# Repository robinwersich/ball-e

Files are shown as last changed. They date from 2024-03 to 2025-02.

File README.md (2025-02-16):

# Ball-E

This robot was created during the **Robot Engineering Project** of the [University of Tartu](https://ut.ee/et) and aimed to build a robot that can [move and balance on a basketball](https://www.youtube.com/watch?v=eqhnZmMAU6M). The final result can be seen in action [here](https://drive.google.com/file/d/1LnrX0tRvga_g_EQCs7Uyl19VpnJzpEGV/preview).
The main concepts in the project explored are:
- use of omniwheels
- bluetooth remote control
- balancing control logic
- 3D printing
- hardware selection and wiring

<div>
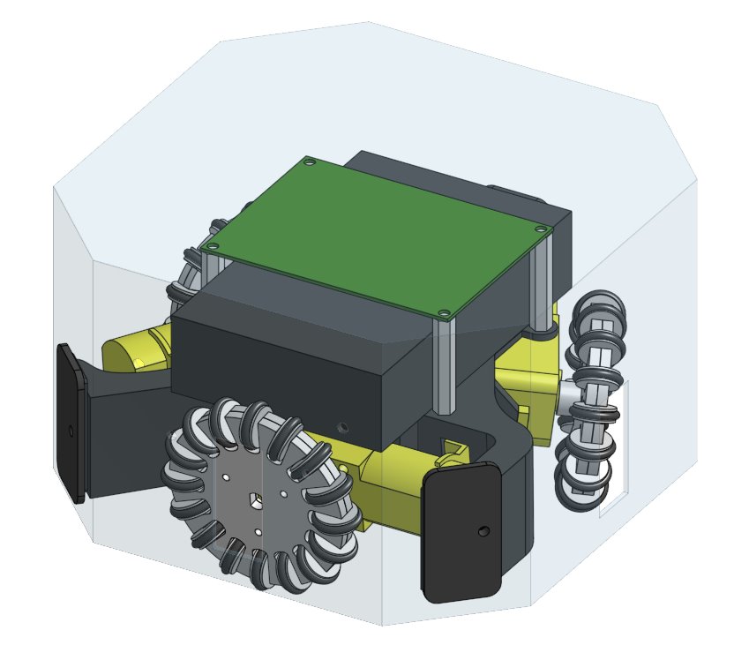
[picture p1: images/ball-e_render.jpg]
  
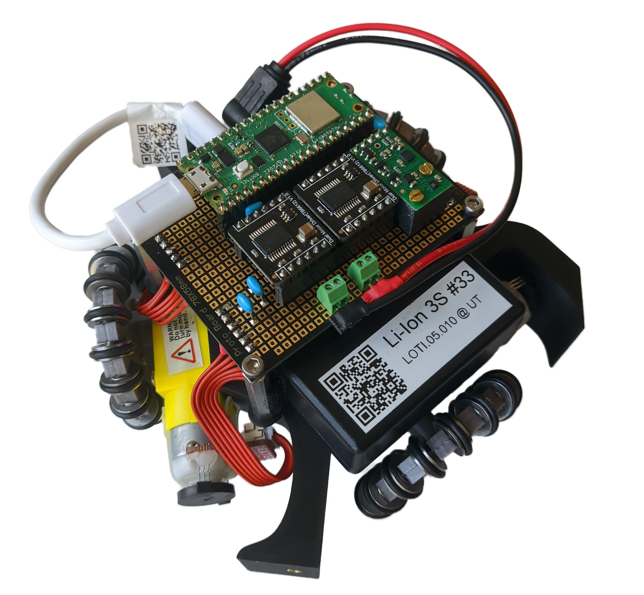
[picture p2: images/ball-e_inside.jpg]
  
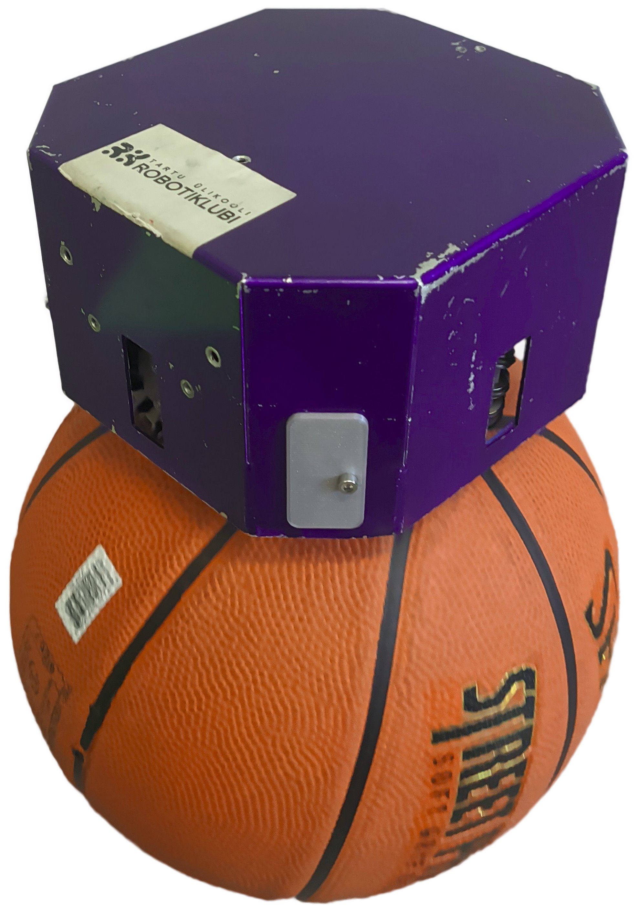
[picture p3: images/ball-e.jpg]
  
</div>

## Hardware BOM

- 3 [motors with encoders](https://gopigo.io/gopigo3-motor-replacement-kit/)
- 3 motor connector cables: 6-pin (0.2mm spacing) to 6-pin (0.254mm spacing), ~8cm length
- 1 [Raspberry Pi Pico W](https://www.raspberrypi.com/products/raspberry-pi-pico/)
- 2 [Dual DC motor drivers](https://www.tme.eu/ee/en/details/df-dri0044/motor-control-modules/dfrobot/dri0044/)
- 1 [IMU](https://www.pololu.com/product/2863)
- 1 12V battery pack
- parts for 3 omniwheels
  - 3 \* 16 small rubber coated wheels similar to [these](https://www.aliexpress.com/item/2054027643.html) (+ axis)
  - 3 \* 3 M2x8  bolts (socket head cap or other non-countersunk) + nuts
- control board
  - [ProtoBoard](https://www.dfrobot.com/product-660.html)
  - 6 10-33nF capacitors
  - 2 screw terminals (2 pins each)
  - MF headers: 2x 20-pin, 2x 14-pin, 1x 5-pin, 3x 6-pin
  - MM headers: 2x 3-pin
  - 2 M2 threaded heat inserts
  - 2 M2x3 bolts (socket head cap or other non-countersunk) for securing the IMU
  - 0.28mm² insulated wire (20cm black, 25cm red, 50cm green, 40cm white)
  - 0.75mm² insulated wire (5cm black, 5cm red)
- battery connector: 9x5x5 barrel jack to 2x2 pin headers, 15cm length, 0.75mm²
- USB-A to Micro-USB cable (ca. 15cm length)
- 6 M3x25 (countersunk or low-profile non-countersunk) and 3 M2.5x15 bolts (socket head cap or other non-countersunk) + nuts for mounting the motors
- 4 M30 FF PCB spacer
- 4 M3 threaded heat inserts
- 10 M3x6 bolts and 1 M3x10 (socket head cap or other non-countersunk) headless bolt for mounting case, pcb and spacers
- 2cm Velcro for attaching battery
- metal case (150x150x90)
- bluetooth gamepad
- size 7 basketball

## 3D printed parts

The following parts are 3D-printed:

- 3x omniwheels (partly)
- robot framework
- IMU mount

A 3D model with all printed and non-printed parts can be found [here](https://cad.onshape.com/documents/aef269c9421a5698f51293a2/w/28d1817e881a7e140ad68222/e/52373abffadf50390ef456f1).
In addition, exported _STEP_ files are available in the `CAD` folder.

## PCB Wiring

The wiring diagram for the PCB can be found in the `wiring` folder. The final result should look similar to this:
<div>
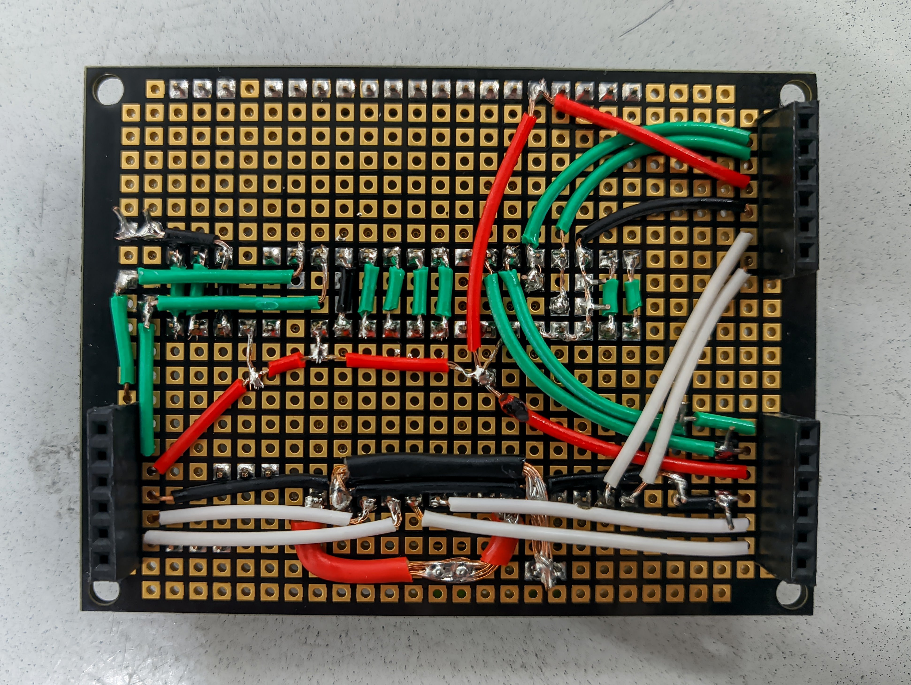
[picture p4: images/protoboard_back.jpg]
  
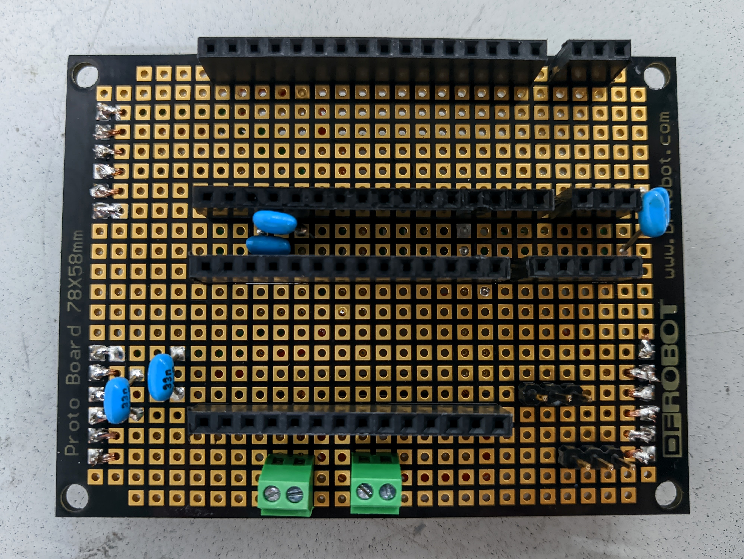
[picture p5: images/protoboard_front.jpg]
  
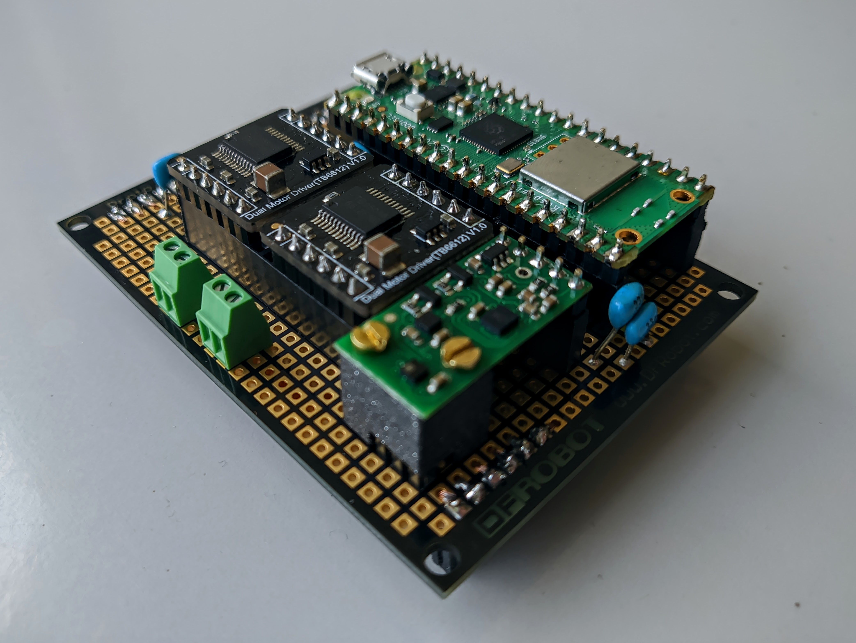
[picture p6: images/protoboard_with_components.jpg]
  
</div>

## Project Code

The Raspberry Pi Pico W is programmed in C++ using the official SDK. As the latter uses [CMake](https://cmake.org/), this project does as well.

### Setup

The following describes the setup using [Visual Studio Code](https://code.visualstudio.com/) but [CLion](https://www.jetbrains.com/de-de/clion/), being CMake-based, should also work well.

1. Set up the Pico SDK using the _Getting Started_ Instructions on the [official website](https://www.raspberrypi.com/documentation/microcontrollers/raspberry-pi-pico.html).
1. Set up the [Bluepad32 library](https://github.com/ricardoquesada/bluepad32) (steps 2 and 3 of this [guide](https://bluepad32.readthedocs.io/en/latest/plat_picow/)).
1. Install the [Eigen](https://eigen.tuxfamily.org/index.php?title=Main_Page) library.
1. Open the repository folder in VS Code. Install the C/C++ Extension and the CMake extension.
1. Set the `PICO_SDK_PATH`, `BLUEPAD32_ROOT` and `Eigen3_DIR` either as global environment variable or in the settings of the CMake extension under _configure environment_.
1. Configure CMake by pressing `Ctrl`+`Shift`+`P` and search for _CMake: configure_. Choose the GCC arm-non-eabi which was installed in Step 1 as compiler. CMake should then automatically be run and create a `build` folder.
   If you run CMake manually, make sure to pass the `-DPICO_BOARD=pico_w` flag.
1. Navigate to the `build` folder and execute `make` to build all project files. Use `-j4` to use 4 threads for a faster build.
1. Connect the Pico while pressing the bootsel button, which should mount is as mass storage device. Then copy the `*.uf2` file to this drive.

### IMU Calibration
The IMU needs to be calibrated for good results:
1. Flash the `playground/imu_calibration` software on the pico.
1. Use the `scripts/imu_calibration.py` script to retrieve the magnetometer and gyro bias, as well as accelerometer measurements.
1. Use [Magneto](https://sailboatinstruments.blogspot.com/2011/09/improved-magnetometer-calibration-part.html) or a similar tool to get the bias and correction matrix for the accelerometer.
1. Adjust the values in `imu_calibration_values.h` correspondingly.

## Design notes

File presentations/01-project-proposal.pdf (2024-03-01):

## IDEAS

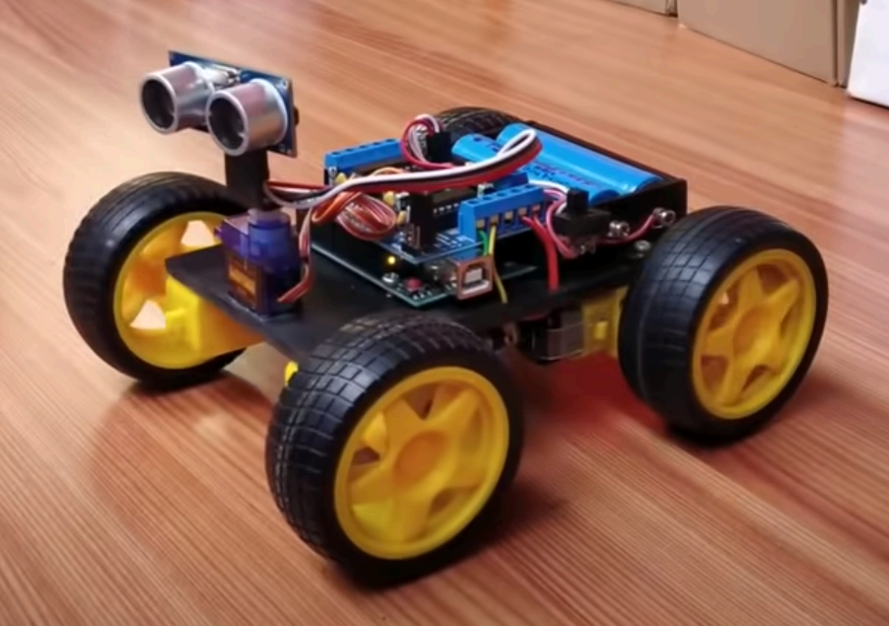
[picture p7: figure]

simple wheels: simple mechanics, simple software

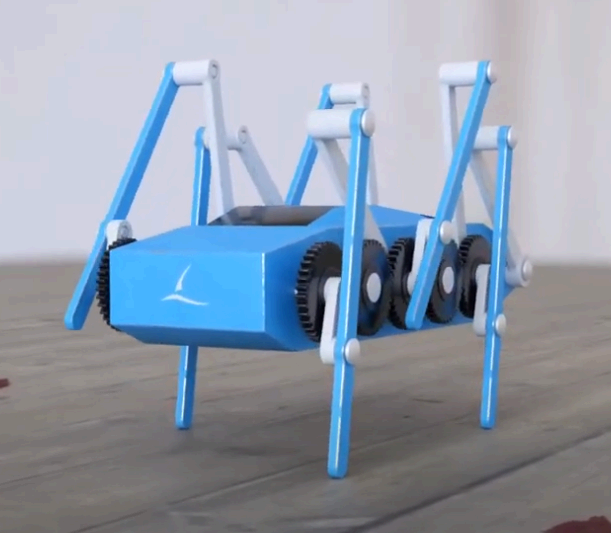
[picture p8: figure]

mechanics-based walking: complex mechanics, simple software

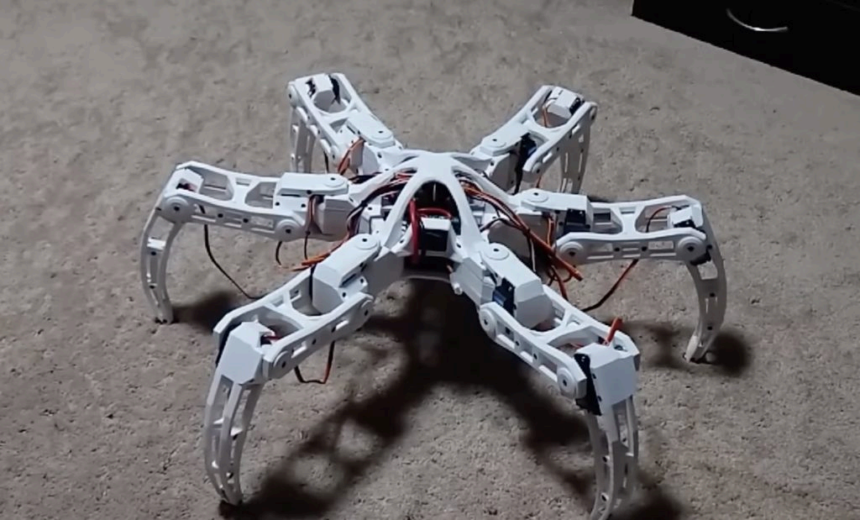
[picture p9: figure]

servo-based walking: medium/complex mechanics, complex software

## I AM A BEGINNER IN ROBOTICS

spider-bot is likely a little over-ambitious (also fitting everything into the given size constraints is hard)
but I also want to do something fancy...

## MIDDLE WAY (ITERATIVE DESIGN)

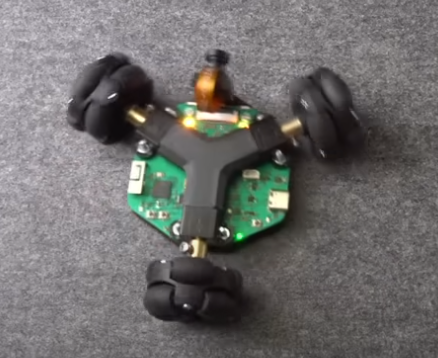
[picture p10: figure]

1st step: omnidirectional wheel robot

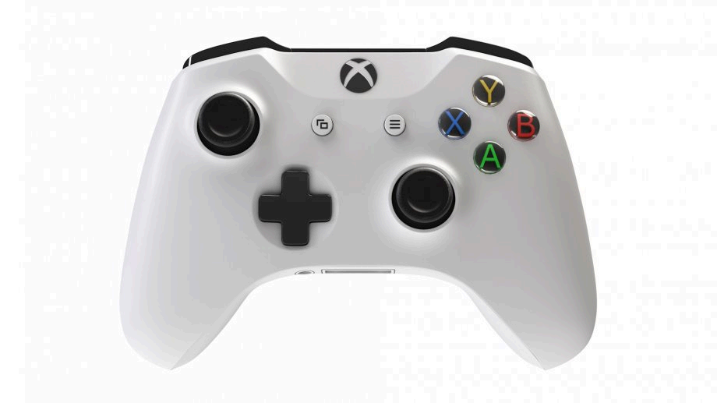
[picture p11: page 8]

2nd step: adding remote control capabilities

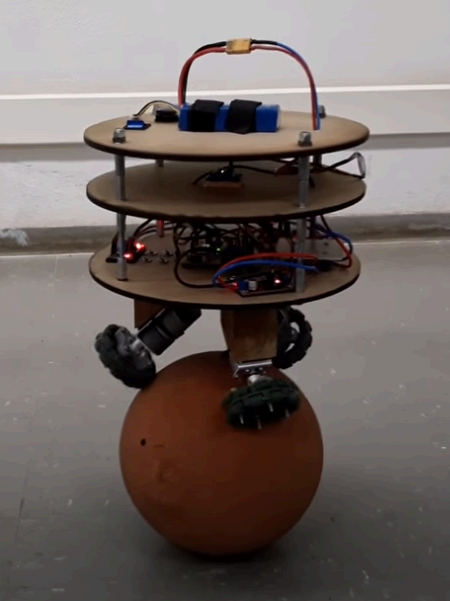
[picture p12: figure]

3rd step (if there's time): add ball balancing capabilities

## FIRST THINGS I NEED TO DO

1. choose hardware (wheels, arduino/raspi, ...)
2. find out how to organize parts in the case
3. build first prototype (learning about printing, soldering etc.)
4. write some basic controller software
5. see how things go from there :)

## BIGGEST CHALLENGE

1. almost all hardware-related (3D printing, soldering, electronics, ...) stuff is new for me
2. getting the robot to balance and still move

## BACKUP

only doing the 1st step
4-wheel robot (not omnidirectional)

# QUESTIONS?

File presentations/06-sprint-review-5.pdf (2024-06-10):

# SPRINT 5

Getting the robot to balance and improving RC

## LAST WEEK

Time spent: 12h
What I learned
My robot survives falling from the ball Magnetometer is more accurate than I thought

## BIGGEST SUCCESS

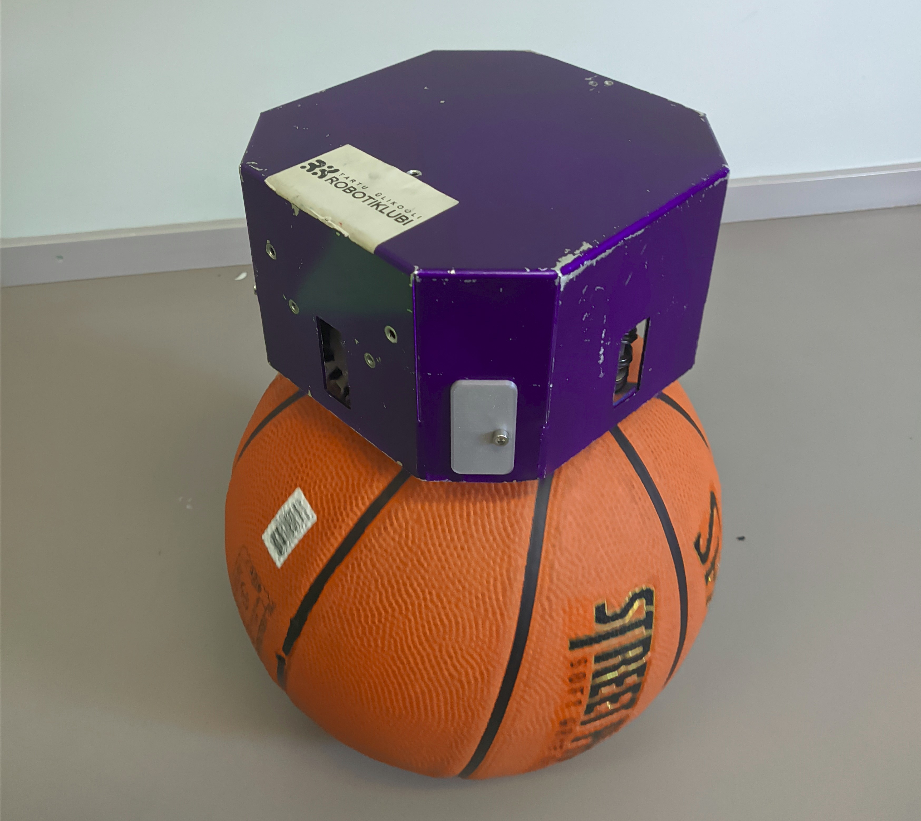
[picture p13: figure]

Make robot balance and move on ball

## BIGGEST FAILURE

Lots of time spent into trying to make it balance more stable without any success

## SPRINT OVERVIEW

Planned:
13 Cards (+2 added after previous done) 33h (+6h) = 39h
Current status:
15 Cards done
41h

## TIME ESTIMATES

10 cards matched exactly
2 cards +0.5h
2 cards +1h (position constraint, advanced movement)
1 card -1h (weekly meeting)

## BEST CARDS

## IMPLEMENT MOVEMENT ON BALL

movement works as expected (even though window to instability is small)

## IMPLEMENT ADVANCED ROBOT CONTROLL

Implementing different movement patterns was fun and took expected time

## WORST CARDS

## FIX VELOCITY MEASUREMENT

unsuccessful (but time boxed, so no overtime) reason: messy hardware signal can't be fixed enough by software (e.g. LP filter)

## FIX BALANCING ISSUES

Various approaches tried
none seemed to produce significant improvements
reason: maybe motors too weak?

# CONCLUSION

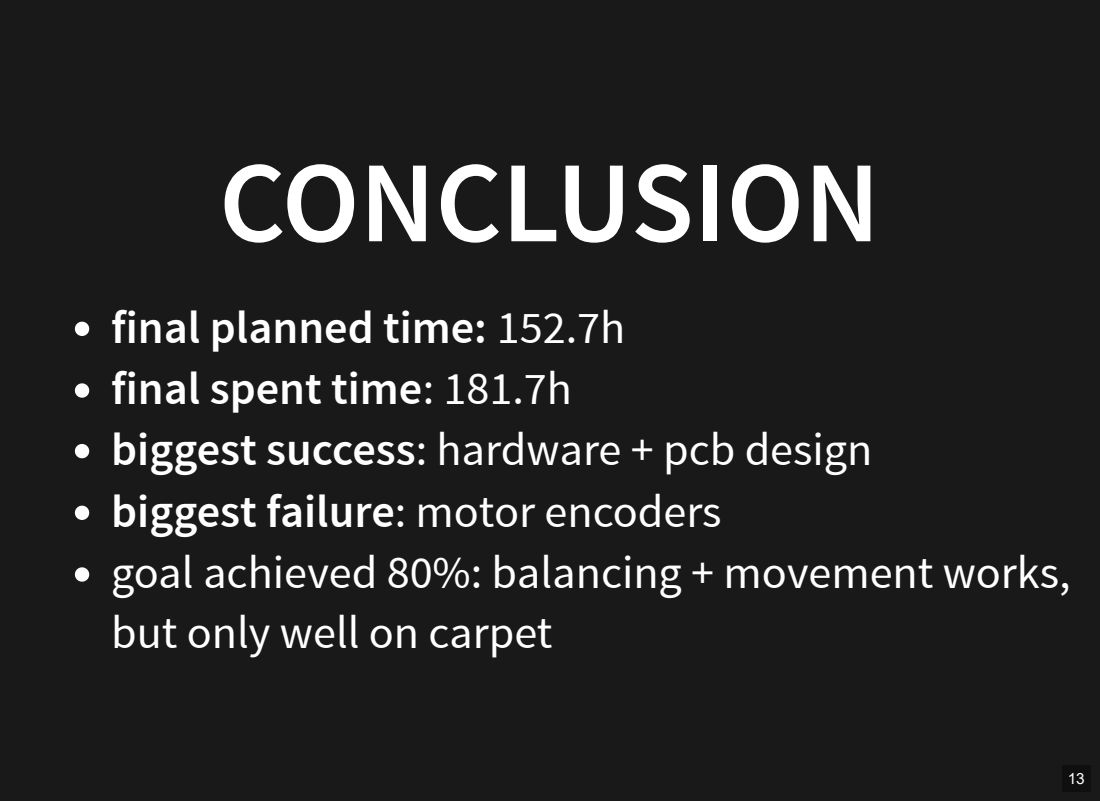
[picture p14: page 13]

final planned time: 152.7h
final spent time: 181.7h
biggest success: hardware + pcb design
biggest failure: motor encoders
goal achieved 80%: balancing + movement works,
but only well on carpet

# FUTURE WORK

Swap motors for stronger ones
Ensure encoders are working properly on them Result: hopefully more stable balancing

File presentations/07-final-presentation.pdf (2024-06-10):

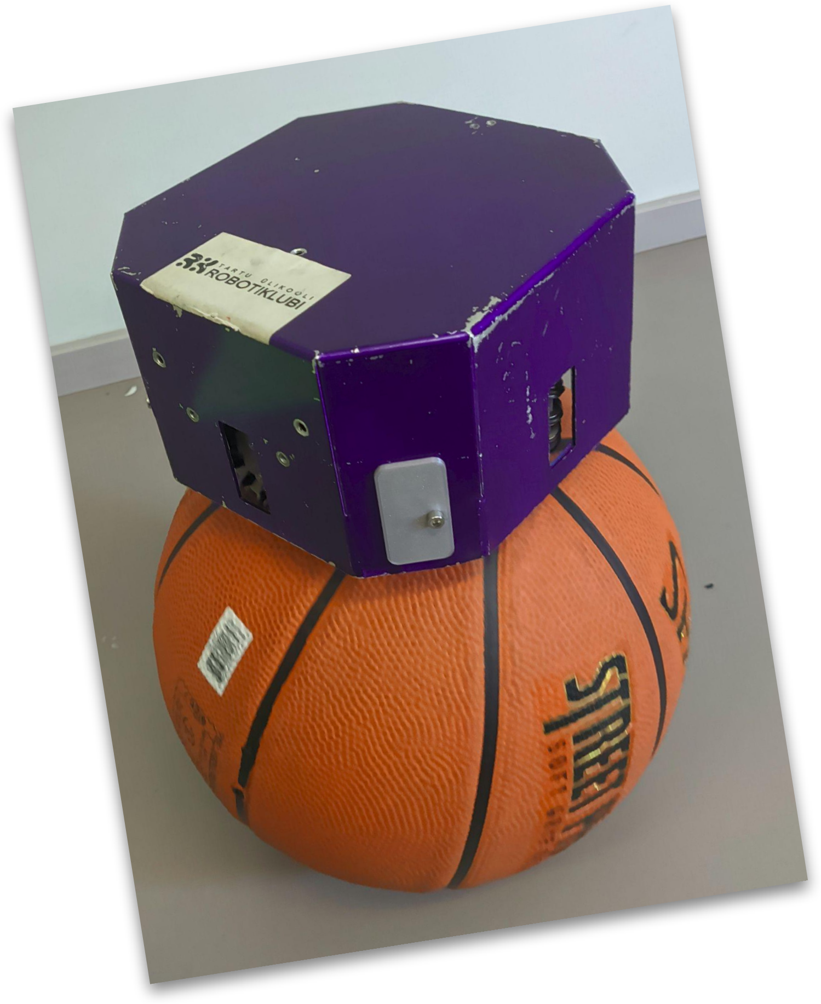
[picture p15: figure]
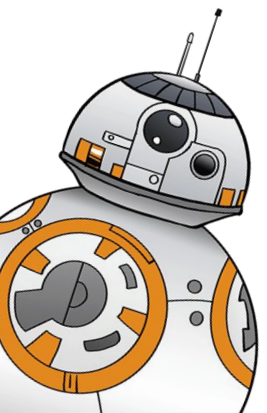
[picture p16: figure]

# BALL-E

A Ball Balancing Robot

# How Can It Move?

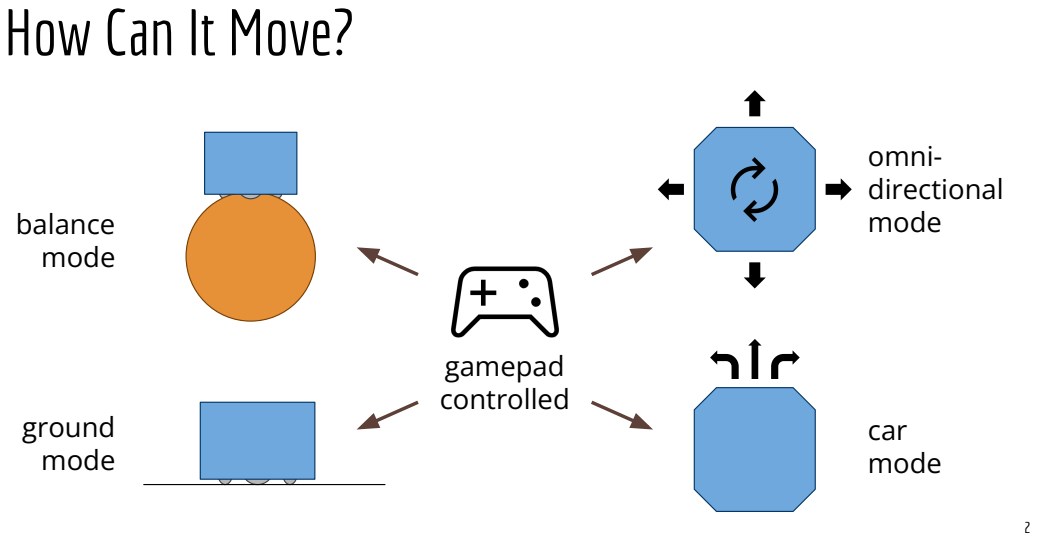
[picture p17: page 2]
gamepad controlled; omni- directional mode; car mode; ground mode; balance mode

# What’s Inside?

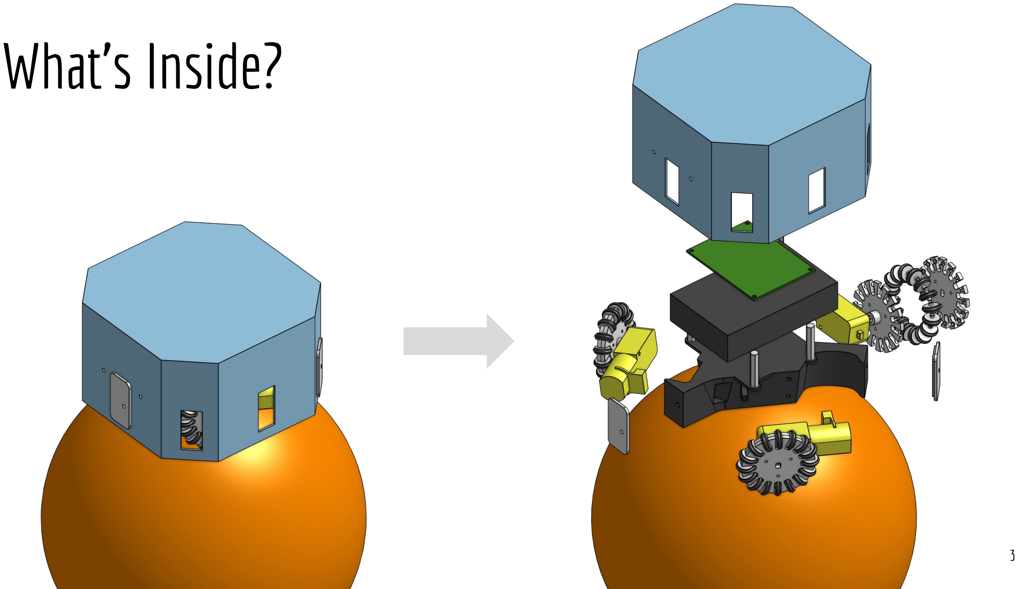
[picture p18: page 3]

# What’s Inside?

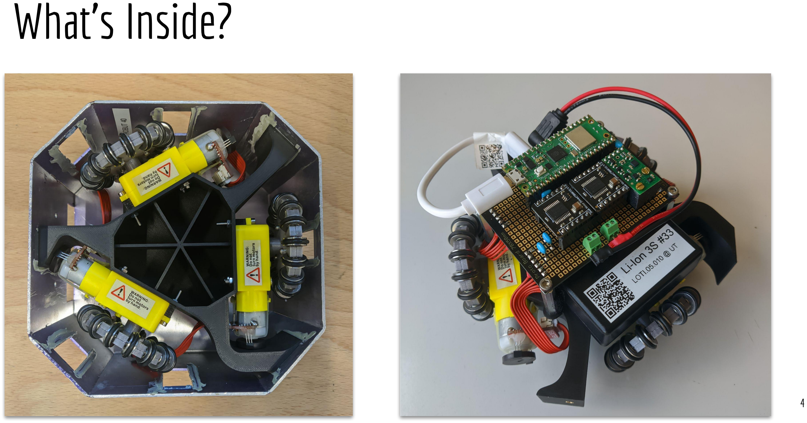
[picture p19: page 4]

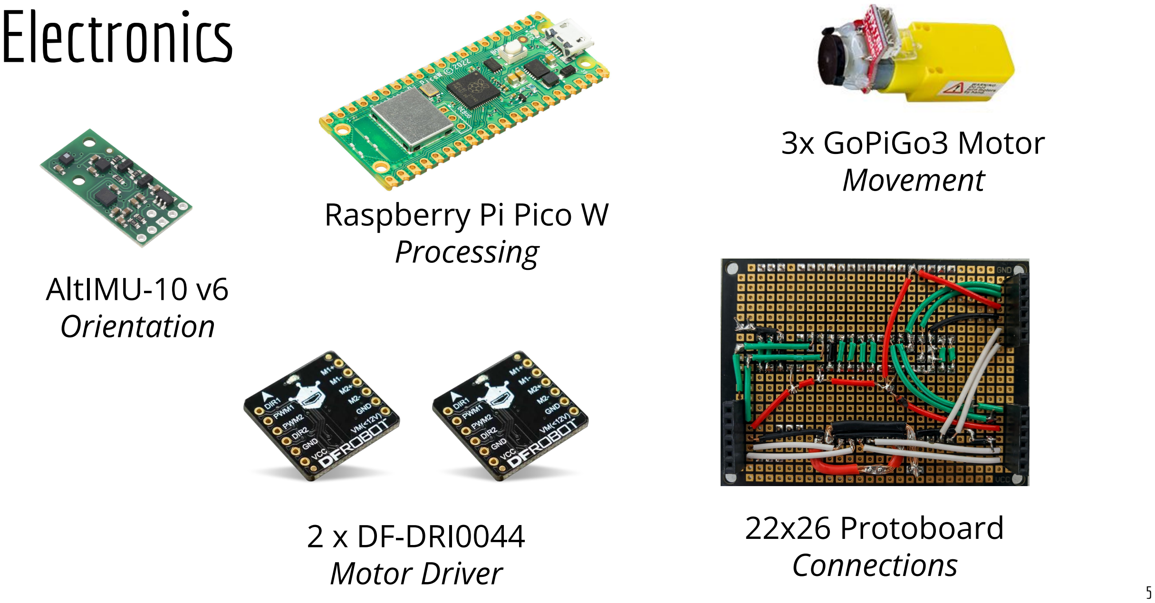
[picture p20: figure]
Electronics; Raspberry Pi Pico W Processing; AltIMU-10 v6 Orientation; 2 x DF-DRI0044 Motor Driver; 22x26 Protoboard Connections; 3x GoPiGo3 Motor Movement

# How Does It Work?

# Omnidirectional Movement

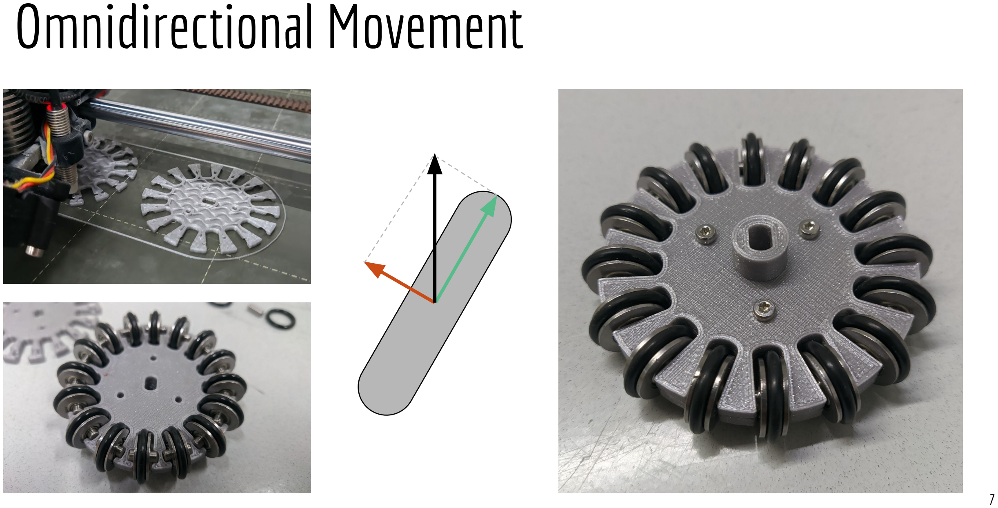
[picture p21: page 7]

# Balancing

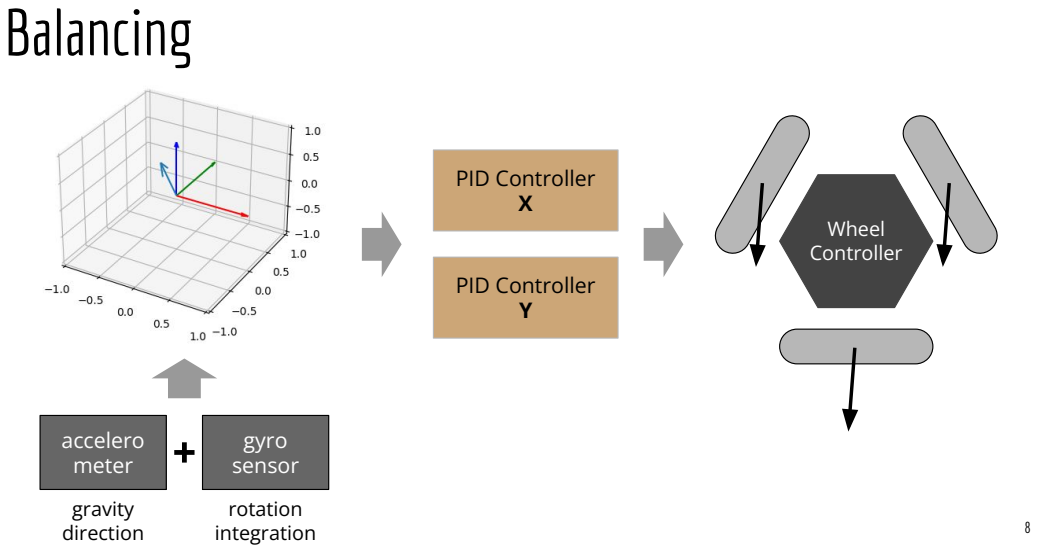
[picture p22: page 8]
accelero meter; gyro sensor; gravity direction; rotation integration; PID Controller X; PID Controller Y; Wheel Controller

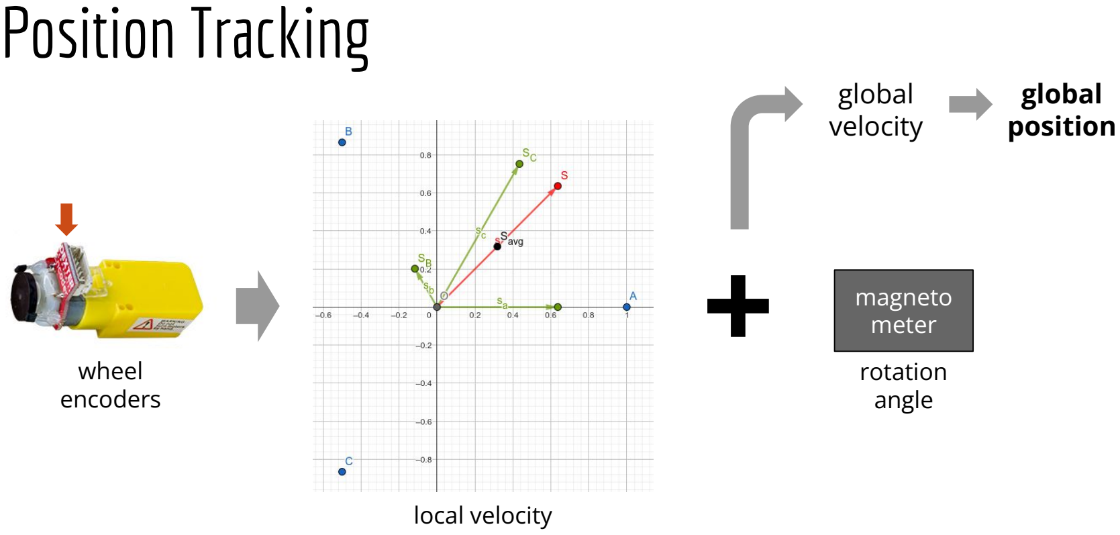
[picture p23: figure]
Position Tracking; magneto meter rotation angle; wheel encoders; local velocity; global velocity; global position

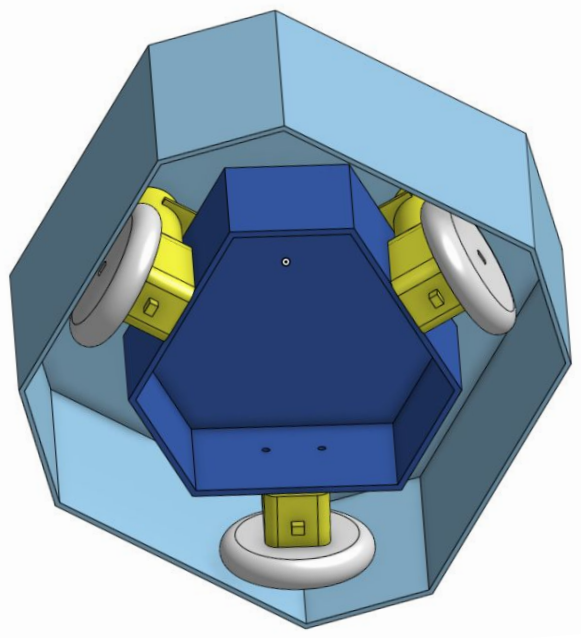
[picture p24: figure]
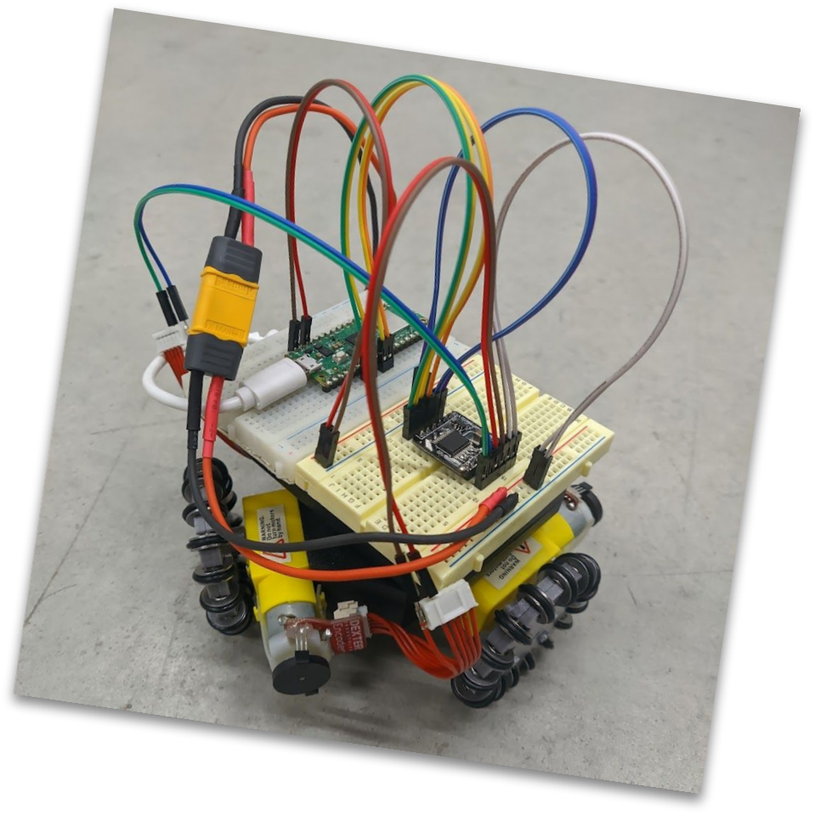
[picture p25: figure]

# Questions?

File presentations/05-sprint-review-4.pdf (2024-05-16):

# SPRINT 4

hardware finalization, orientation measurement, movement and lots of overtime

## LAST WEEK

Time spent: 21.5h
What I learned
much about soldering
protoboards may have VCC/GND lanes... properly integrating angular velocity vectors

## BIGGEST SUCCESS 1

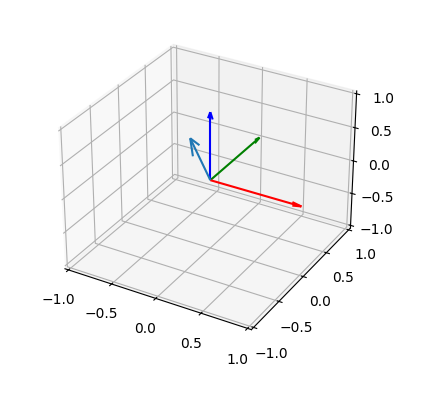
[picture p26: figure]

measuring absolute orientation works well

## BIGGEST SUCCESS 2

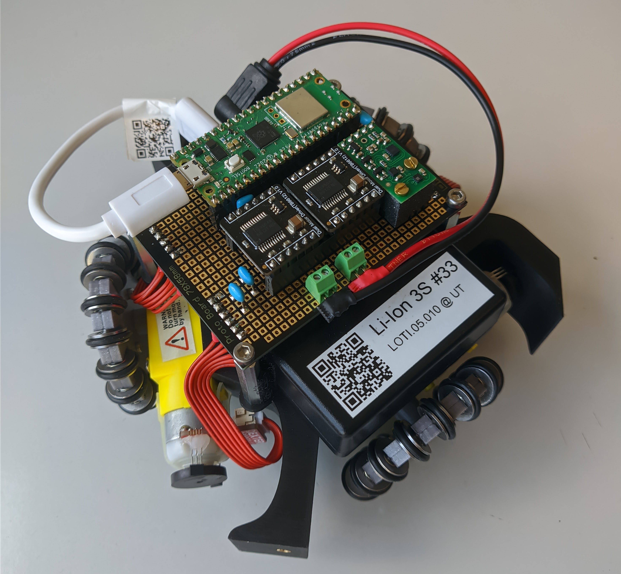
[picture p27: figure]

final hardware - but getting there was hard...

## BIGGEST FAILURE

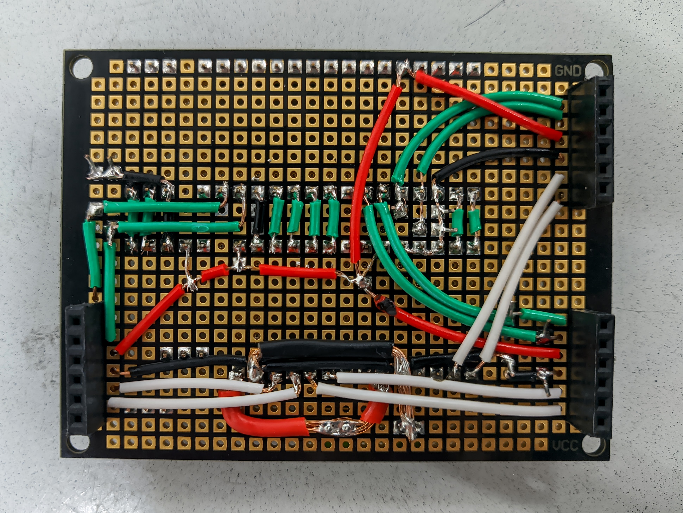
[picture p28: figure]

soldering protoboard took much longer than expected but turned out nice...

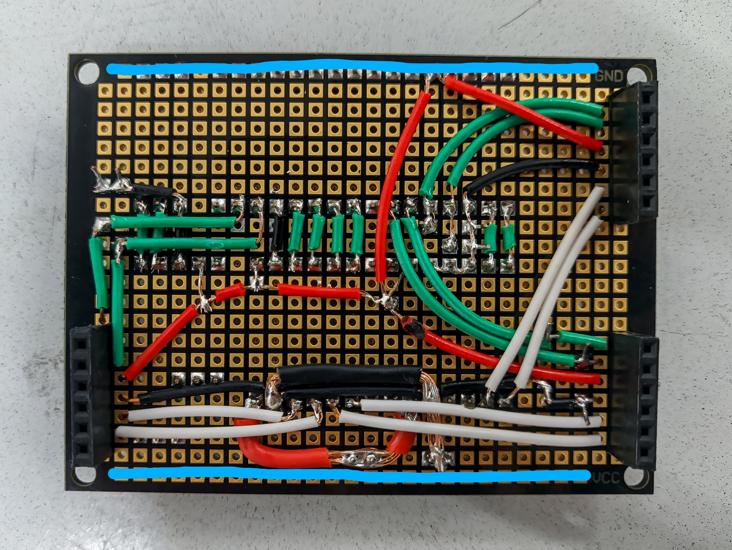
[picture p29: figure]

...until I realised protoboard trolled me :/

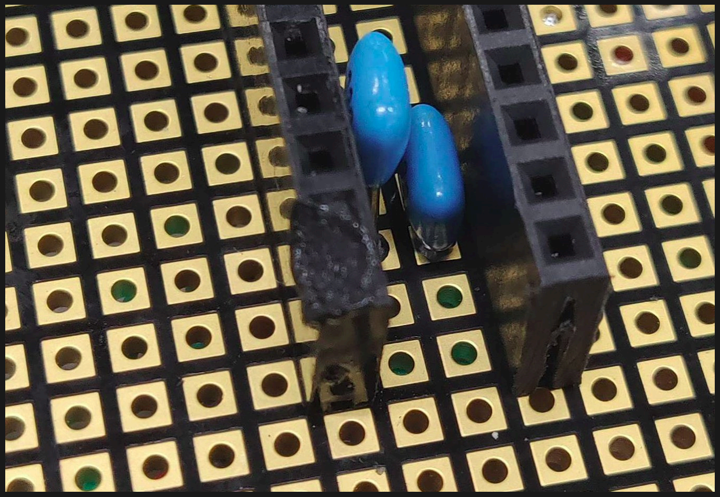
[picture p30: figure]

...and I melted a pin header in the process of trying to fix it but Jako helped me fix it ❤️

## SPRINT OVERVIEW

Planned:
17 Cards
33.5h
Current status:
16 Cards done, 1 card not finished 51.5h 😅

## TIME ESTIMATES


9 cards matched exactly
3 cards +1h
2 cards -0.5 - -1.5h (research)
Design Framework v3: 3h -> 8h
Connect IMU: 1.5h -> 5h
Solder Protoboard: 2.5h -> 12h

## BEST CARDS

## MAKE GAMEPAD CONTROL ROBOT


implementation was straightforward and result very satisfying

## MEASURE ROBOT ORIENTATION

worked well and learned much

## WORST CARDS

## CONNECT IMU

4h instead of 1.5
reasons:
overwhelmed by large interface interface more low-level than expected

## SOLDER PROTOBOARD

Soldering took very long
Made some non-easily fixable mistakes reasons:
overconfidence (soldering pin headers worked well but wires are much harder) missing experience (could have prevented overseeing ground rail and melting pin header)

# LAST SPRINT

will be though
still have encoder issues
IMU is not yet calibrated
tuning PIDs can take indefinitely long

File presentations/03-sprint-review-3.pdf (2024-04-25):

# SPRINT 3

a lot of invisible work

## LAST WEEK

Time spent: 18.5h
What I learned
Encoder pitfalls
animations in matplotlib
bluepad32 wireless gamepad library CMake pitfalls

## BIGGEST SUCCESS

Bluetooth connection establishment :D (took a while, but could have been much worse)

## BIGGEST FAILURE

Trying to write a motor PID controller (it's much more difficult than I thought)

## SPRINT OVERVIEW

Planned:
12 Cards
27h
Current status:
11 Cards done, 1 card backlog 29h

## TIME ESTIMATES

4 cards matched exactly
4 cards ± 0.5h
1 card + 4h :/

## BEST CARDS

## ADD 3RD MOTOR & MAKE 6-PIN CONNECTORS


omnidirectional movement works very well :D

## MAKE PLOTTING/PID TUNING UTILITY


dynamic setting of parameters and simultaneous plotting help a lot

## WORST CARDS

## IMPLEMENT ENCODER PROCESSING

2h instead of 1
reasons:
interrupt handling less straightforward then expected in C++

## IMPLEMENT MOTOR PID CONTROLLER

Implementation done almost in time (2.5h) But debugging took much longer than expected (and controller still not fully working)
reasons:
wrong assumptions about encoders underestimated PID complexity


## NEXT SPRINT THE WORK WILL PAY OFF :)

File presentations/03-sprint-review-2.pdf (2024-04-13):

## LAST 2 WEEKS

Time spent: 18.5h
What I learned:
How to draw circuit diagrams GPIO number != PIN number
M3 fits through 2.9mm hole! Plan your delivery times!

## SPRINT OVERVIEW

Planned:
14 Cards
30h
Current status:
13 Cards done, 1 card backlog 31h

## TIME ESTIMATES

7 cards matched exactly
2 cards ± 0.5h
4 card + 1-1.5h (motor / robot control, framework / circuit design)

## BEST CARDS

## PRINT & ASSEMBLE OMNIWHEELS


no problems because of previous test print

## ASSEMBLE FIRST PROTOTYPE


because of previous CAD and circuit design everything fit well

## WORST CARDS

## MAKE PICO CONTROL ONE MOTOR

took much longer than expected reasons:
unfamiliarity with pico pins harware debugging is difficult

## DESIGN FRAMEWORK V2

spend much time just thinking reasons:
too little out-of-the-box thinking
too large steps (already wanted to include PCB)



## BIGGEST SUCCESS

Moving Robot (Live Demo) :D

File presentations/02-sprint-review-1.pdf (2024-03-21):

## OVERVIEW

Planned:
12 Cards
28.7h
Current status:
11 Cards done, 1 blocked
29.2h

## TIME ESTIMATES

4 cards matched exactly
5 cards +0.5h
1 card +1.5h (Pico setup)
1 card -0.3h

## BEST CARDS

choose CAD software & get familiar 2h limit avoided paralysis by analysis model first version of robot
again, timelimit doing too much detail got valuable insights for space in robot still got time to do other things

## WORST CARDS

make Pico control one motor blocked until sprint end (no battery) reason: bad communication? print robot frame v1
v1 was not ready for physical print had to print something else (wheels) required out-of sprint modelling time

## BIGGEST FAILURE


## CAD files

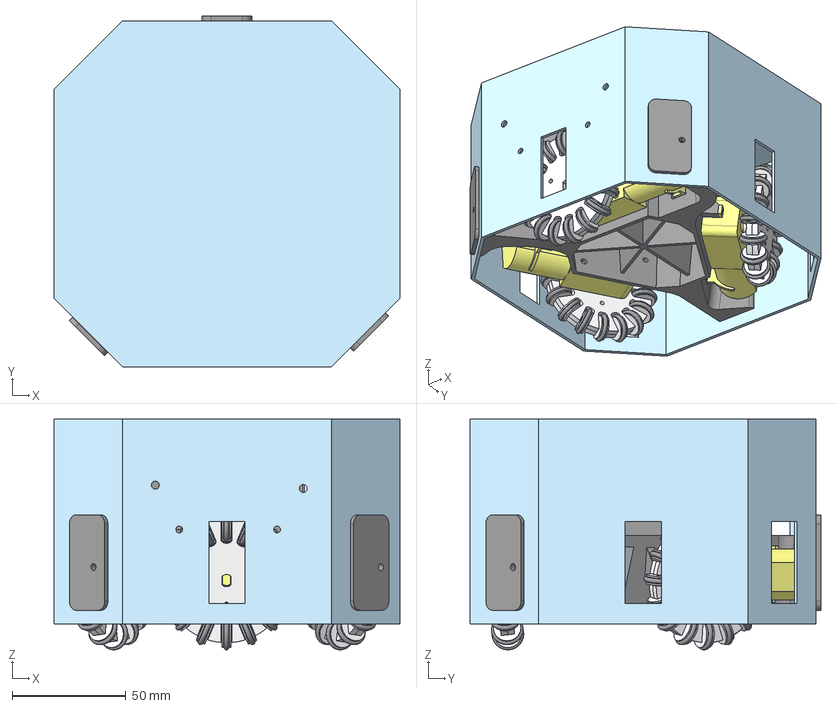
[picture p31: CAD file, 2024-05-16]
CAD/Robot.step
152.0 x 154.0 x 101.4 mm
Spacer x 4
Case
Case Plug 2
Case Plug 3
Battery
Motor x 3
Case Plug 1
PCB
Metal Wheel x 48
O Ring x 48
Wheel Top x 3
Wheel Bottom x 3
Frame

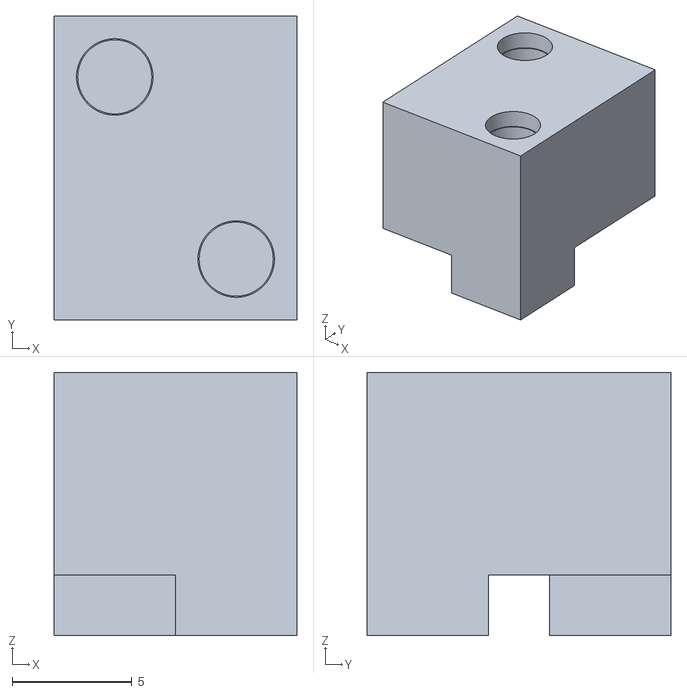
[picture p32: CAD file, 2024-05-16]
CAD/Robot Parts - IMU Adapter.stl
10.2 x 12.7 x 11.0

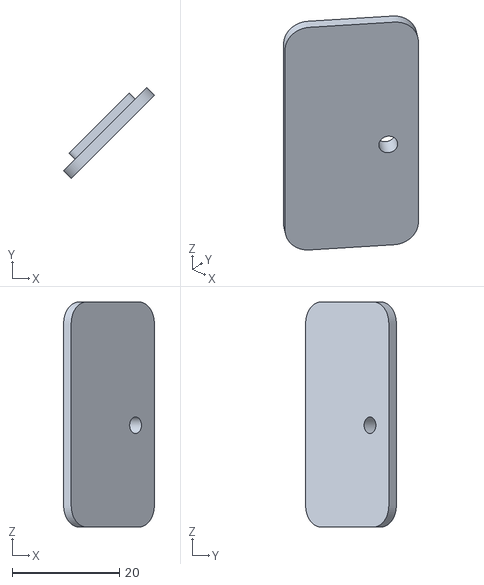
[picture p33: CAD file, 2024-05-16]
CAD/Robot Parts - Case Plug 2.stl
16.9 x 16.9 x 41.9

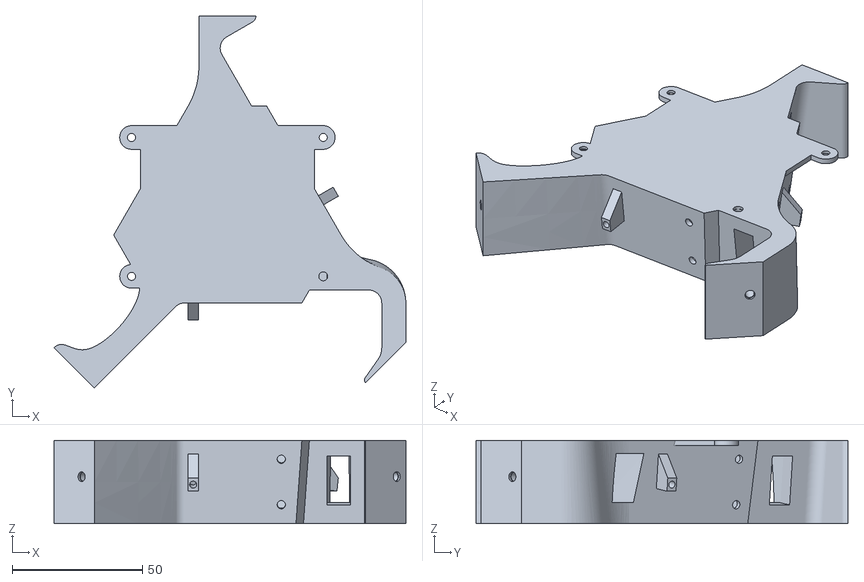
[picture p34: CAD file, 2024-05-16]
CAD/Robot Parts - Frame.stl
135.2 x 143.0 x 32.0

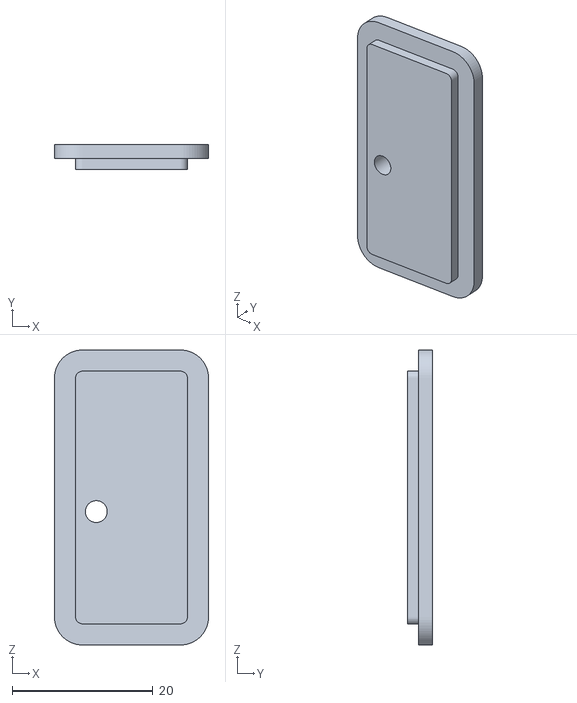
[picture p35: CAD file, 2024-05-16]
CAD/Robot Parts - Case Plug 3.stl
21.9 x 3.60 x 41.9

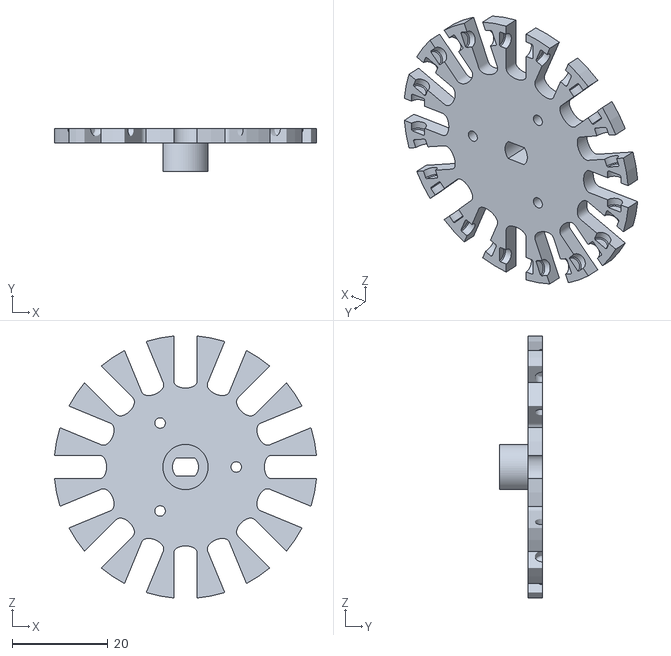
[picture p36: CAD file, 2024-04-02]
CAD/Robot Parts - Wheel Top.stl
54.8 x 9.00 x 54.8

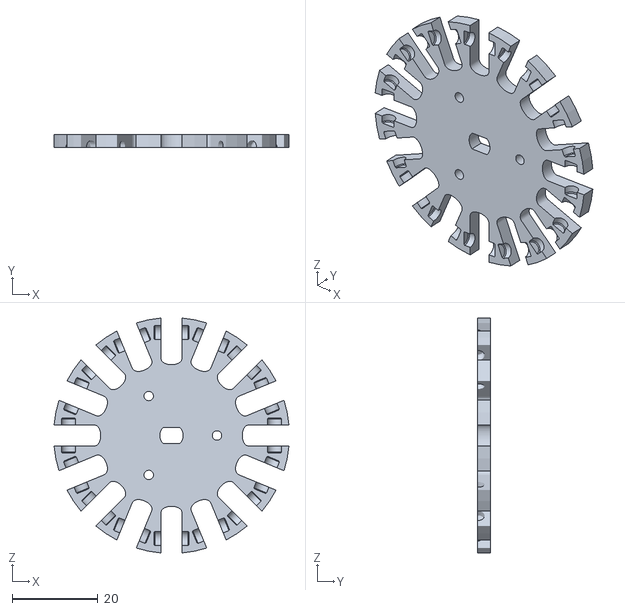
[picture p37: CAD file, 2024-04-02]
CAD/Robot Parts - Wheel Bottom.stl
54.8 x 3.00 x 54.8

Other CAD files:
CAD/Robot Parts - Case Plug 1.stl

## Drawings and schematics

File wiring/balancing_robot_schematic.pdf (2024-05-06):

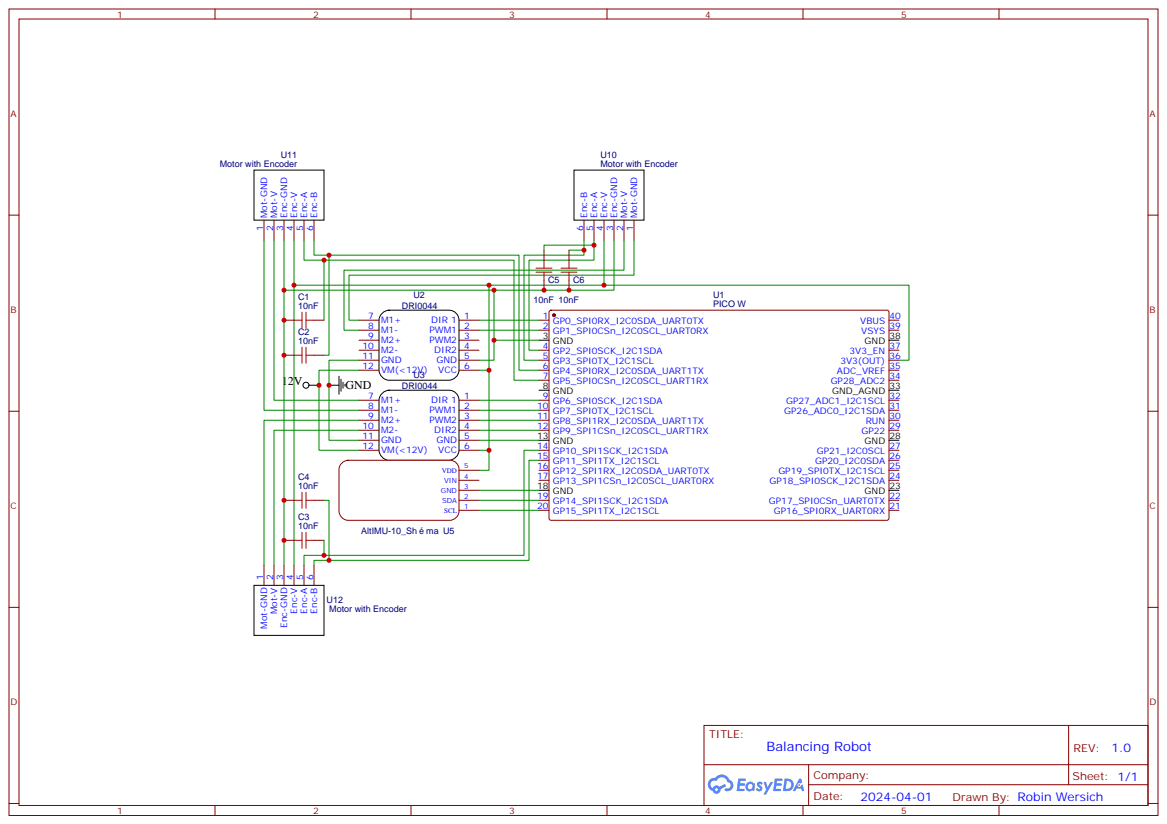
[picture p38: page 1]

Drawn By: Robin Wersich

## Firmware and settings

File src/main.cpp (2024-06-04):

#include "btcontrol.h"
#include "imu_calibration_values.h"
#include "motor_driver_kickstart.h"
#include "motor_drivers/dri0044.h"
#include "pico/critical_section.h"
#include "pico/stdlib.h"
#include "robot.h"
#include "robot_control.h"

const uint PWM_FREQUENCY = 25000;
// -- motor 1 --
const uint DIR1 = 0;
const uint PWM1 = 1;
const uint ENC1_SLOT = 1;
// -- motor 2 --
const uint DIR2 = 6;
const uint PWM2 = 7;
const uint ENC2_SLOT = 2;
// -- motor 3 --
const uint PWM3 = 8;
const uint DIR3 = 9;
const uint ENC3_SLOT = 5;
// -- IMU --
const uint IMU_SLOT = 7;

int main() {
  stdio_init_all();

  // configure hardware timers to have lower priority than the default
  irq_set_priority(TIMER_IRQ_0, PICO_DEFAULT_IRQ_PRIORITY + 1);
  irq_set_priority(TIMER_IRQ_1, PICO_DEFAULT_IRQ_PRIORITY + 1);
  irq_set_priority(TIMER_IRQ_2, PICO_DEFAULT_IRQ_PRIORITY + 1);
  irq_set_priority(TIMER_IRQ_3, PICO_DEFAULT_IRQ_PRIORITY + 1);

  // setup IMU
  sleep_ms(100);
  LSM6::AccelConfig accel_config{
    .odr = lsm6::odr::HZ_104, .fs = lsm6::fs::acc::G_2, .lp_cutoff = lsm6::cutoff::accel::CO_45
  };
  LSM6::GyroConfig gyro_config{
    .odr = lsm6::odr::HZ_104,
    .fs = lsm6::fs::gyro::DPS_1000,
    .lp_intensity = lsm6::cutoff::gyro::CO_7
  };
  const auto i2c_port = init_i2c_port(IMU_SLOT, LSM6::MAX_BAUDRATE);
  const auto lsm6 = std::make_shared<LSM6>(
    i2c_port, accel_config, gyro_config, true, LSM6_CALIBRATION,
    Eigen::Matrix3f{{0, 1, 0}, {-1, 0, 0}, {0, 0, 1}}
  );
  const auto lis3 = std::make_shared<LIS3>(
    i2c_port, LIS3::MagnetometerConfig{.odr = lis3::odr::HZ_155, .fs = lis3::fs::GS_4}, true,
    LIS3_CALIBRATION, Eigen::Matrix3f{{0, 1, 0}, {-1, 0, 0}, {0, 0, 1}}
  );
  sleep_ms(100);

  // setup motor drivers
  Kickstart kickstart{.start_threshold = 0.4, .end_threshold = 0.15, .duration_ms = 10};
  auto driver_1 = std::make_unique<KickstartMotorDriver>(
    std::make_unique<MotorDriverDRI0044>(PWM1, DIR1, PWM_FREQUENCY, true), kickstart
  );
  auto driver_2 = std::make_unique<KickstartMotorDriver>(
    std::make_unique<MotorDriverDRI0044>(PWM2, DIR2, PWM_FREQUENCY), kickstart
  );
  auto driver_3 = std::make_unique<KickstartMotorDriver>(
    std::make_unique<MotorDriverDRI0044>(PWM3, DIR3, PWM_FREQUENCY), kickstart
  );

  // setup motor decoders
  MotorDecoder decoder_1{ENC1_SLOT, true};
  MotorDecoder decoder_2{ENC2_SLOT};
  MotorDecoder decoder_3{ENC3_SLOT, true};

  // setup speed config
  SpeedConfig speed_config(750 / M_PI / 2, 30.95, 57.46, 30.576, 54.277, 100);

  // setup robot
  Robot robot{
    std::array<Omniwheel, 3>{
      Omniwheel(30, std::move(driver_1), MotorState{&decoder_1.state(), 6, 115}),
      Omniwheel(150, std::move(driver_2), MotorState{&decoder_2.state(), 6, 115}),
      Omniwheel(270, std::move(driver_3), MotorState{&decoder_3.state(), 6, 115})
    },
    OrientationEstimator{lsm6, lis3},
    PidGains{15.0, 500.0, 0.0},
    2.5,
    speed_config,
    LowPassCoefficients{.a1 = 0.85956724, .b0 = 0.07021638, .b1 = 0.07021638},
    LowPassCoefficients{.a1 = 0.97024184, .b0 = 0.01487908, .b1 = 0.01487908}
  };

  // setup robot controller
  RobotController controller{&robot};
  RobotController::initialize_controller(&controller);

  // start controll loops
  robot.start_updating();
  controller.run_loop();

  return 0;
}

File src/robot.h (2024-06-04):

#pragma once

#include <Eigen/Core>
#include <limits>

#include "omniwheel.h"
#include "orientation_estimator.h"
#include "pico/critical_section.h"
#include "pico/time.h"
#include "pid.h"

struct SpeedConfig {
  /** How many meters one wheel rotation corresponds to on the ground. */
  float ground_m_per_rev;
  /** How many meters one wheel rotation corresponds to on the ball. */
  float balance_m_per_rev;
  /** How many radians of rotation one wheel rotation corresponds to on the ground. */
  float ground_rad_per_rev;
  /** How many radians of rotation one wheel rotation corresponds to on the ball. */
  float balance_rad_per_rev;
  /** How long the distance between speed measurement updates should be. */
  uint32_t update_period_ms;

  /**
   * Creates a speed configuration from various measurements (all in mm).
   * @param ball_radius The radius of the ball.
   * @param ground_wheel_radius The distance between the wheel axis and ground contact point.
   * @param gound_circle_radius The distance between the wheel contact point and robot center.
   * @param ball_wheel_radius The distance between the wheel axis and ball contact point.
   * @param ball_circle_radius The distance between the ball contact point and robot center.
   */
  SpeedConfig(
    double ball_radius, double ground_wheel_radius, double ground_circle_radius,
    double ball_wheel_radius, double ball_circle_radius, uint32_t update_period_ms
  );
};

class Robot {
 public:
  /**
   * Creates a new robot instance.
   * @param wheels The three omniwheels of the robot.
   * @param orientation_estimator The orientation estimator to use for balancing.
   * @param pid_gains The PID gains to use for balancing.
   *  Units are S/g, S/(g·s), and S/(g/s) for kp, ki, and kd respectively
   *  where S is the speed fraction of the robot and g is the gravity influence on each axis
   * @param encoder_gain The gain with which to add the current speed (rps) to the balance output.
   * @param max_tilt The maximum tilt the robot can still recover from in degrees.
   * @param speed_config The configuration for converting wheel rotations to meters and radians.
   * @param orientation_filter An optional low-pass filter to apply to the orientation derivative.
   * @param balance_speed_filter An optional low-pass filter to apply to the speed when balancing.
   * @note The robot will not start moving until `start_updating` is called.
   */
  Robot(
    std::array<Omniwheel, 3> wheels, OrientationEstimator orientation_estimator, PidGains pid_gains,
    float max_tilt, const SpeedConfig& speed_config,
    const LowPassCoefficients& orientation_filter = {},
    const LowPassCoefficients& balance_speed_filter = {}
  );
  ~Robot();

  /**
   * Make the robot drive in the direction and with the speed given by the movement vector.
   * The length of the movement vector should be between 0 and 1.
   * @param x The rightward component of the movement vector.
   * @param y The forward component of the movement vector.
   * @param is_global If the speed is given in global coordinates.
   */
  void set_drive_speed(float x, float y, bool is_global = false);

  /**
   * Make the robot rotate around its center.
   * @param speed The speed at which to rotate, between -1 (clockwise) and 1 (anti-clockwise).
   */
  void set_rotate_speed(float speed);

  /**
   * Sets linear drive and rotational speed at once.
   * @param x The rightward component of the movement vector.
   * @param y The forward component of the movement vector.
   * @param speed The speed at which to rotate, between -1 (clockwise) and 1 (anti-clockwise).
   * @param is_global If the speed is given in global coordinates.
   */
  void set_speed(float x, float y, float rot, bool is_global = false);

  /** Stops the robot. */
  void stop();

  /** Enables or disables the ball balancing mode. */
  void set_balancing(bool enabled);
  /** Toggles the ball balancing mode. */
  void toggle_balancing();
  /** Returns true if the robot is currently balancing. */
  bool is_balancing() const;

  /** Sets up a timer interrupt for handling the robot movement. */
  void start_updating();
  /** Stops the timer interrupt for handling the robot movement. */
  void stop_updating();

  /** Sets the current position estimate in meters. */
  void set_position(const Eigen::Vector2f&);
  /** Sets the current angle estimate in radians. */
  void set_angle(float radians);
  /** Sets the maximum distance the robot is allowed to move from the global origin in meters. */
  void set_max_distance(float max_distance);
  /** Sets the maximum ground speed fraction the robot is allowed to move. */
  void set_max_ground_speed(float speed);
  /** Sets the maximum rotation speed fraction the robot is allowed to rotate. */
  void set_max_rotation_speed(float speed);
  /** Sets the maximum tilt the robot can still recover from in degrees. */
  void set_max_tilt(float max_tilt);

  /** Returns the PID controller for the x-axis  */
  PidController& pid_x() { return _pid_x; }
  /** Returns the PID controller for the y-axis  */
  PidController& pid_y() { return _pid_y; }

 private:
  float _speed_to_balance_factor;   // factor for converting speed vector to balance target vector
  float _max_ground_speed = 1.0;    // input speed fraction
  float _max_rotation_speed = 1.0;  // input speed fraction
  std::array<Omniwheel, 3> _wheels;
  OrientationEstimator _orientation_estimator;
  PidController _pid_x, _pid_y;
  LowPassFilter _balance_speed_filter_x;
  LowPassFilter _balance_speed_filter_y;
  bool _is_speed_global = false;
  float _squared_max_distance = std::numeric_limits<float>::infinity();
  Eigen::Vector2f _target_speed = {0, 0};    // fractional speed, local or global
  float _target_rotation = 0;                // fractional speed
  bool _is_translating = false;              // whether there currently is a translation signal
  bool _is_rotating = false;                 // whether there currently is a rotation signal
  Eigen::Vector2f _measured_speed = {0, 0};  // rps, local
  float _measured_rotation = 0;              // rps
  float _current_angle = 0;                  // radians
  Eigen::Vector2f _current_position;         // meters, global
  float _angle_offset = 0;                   // radians
  SpeedConfig _speed_config;
  bool _balancing_mode = false;
  repeating_timer_t _balance_update_timer;
  repeating_timer_t _speed_update_timer;
  critical_section_t _cs;
  uint32_t _last_update_us = 0;

  /** Resets values that are updated while balancing */
  void reset_balancing();

  /** Updates the robot's orientation and movement (based on the current movement goal) */
  void update();
  /** Updates the robots movement based on the desired speed */
  void update_ground();
  /** Updates the robots movement based goal of balancing and achieving the desired speed */
  void update_balancing();
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

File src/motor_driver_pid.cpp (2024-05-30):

#include "motor_driver_pid.h"

MotorDriverPid::MotorDriverPid(
  std::unique_ptr<MotorDriver> driver, const MotorDecoderState* decoder_state, MotorSpec motor_spec,
  PidGains pid_gains, const LowPassCoefficients& filter, const char* name
)
  : _driver{std::move(driver)}
  , _max_speed{motor_spec.max_rpm}
  , _controller{-1.0, 1.0, pid_gains, {}, name}
  , _motor_state{
      decoder_state, motor_spec.ticks_per_revolution, motor_spec.gear_ratio, filter
    } {
  add_repeating_timer_ms(
    MotorDriverPid::sample_time_millis,
    [](repeating_timer_t* timer) {
      auto driver = static_cast<MotorDriverPid*>(timer->user_data);
      driver->update_controller();
      return true;
    },
    this, &this->_update_timer
  );
}

MotorDriverPid::~MotorDriverPid() { cancel_repeating_timer(&_update_timer); }

void MotorDriverPid::drive_rpm(float rpm) { _controller.set_target(rpm / 60); }
void MotorDriverPid::drive(float speed) { drive_rpm(speed * _max_speed); }

PidController& MotorDriverPid::controller() { return _controller; }

void MotorDriverPid::update_controller() {
  const auto rps = _motor_state.compute_speed_rps();
  const auto output = _controller.compute(rps);
  _driver->drive(output);
}

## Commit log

2024-03-25 Add wheel CAD model
    [Robot Parts - Wheel Bottom.stl, Robot Parts - Wheel Top.stl]
2024-03-28 Add robot model file
    [Robot Parts - Wheel Bottom.stl, Robot Parts - Wheel Top.stl, Robot.step]
2024-03-28 Add connection diagram for motor test
    [motor_test.fzz]
2024-03-28 Remove gcode folder
    [Robot.step]
2024-04-01 Add circuit schematic
    [motor_test.fzz]
2024-04-02 Update robot CAD
    [Robot Parts - Frame.stl, Robot Parts - Wheel Bottom.stl, Robot Parts - Wheel Top.stl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]
2024-04-08 Extract motor wrapper
2024-04-08 Create motor driver interface
2024-04-08 Add DRI0044 driver
2024-04-08 Make motor driver interface more elegant
2024-04-08 Move motor driver interface to top level
2024-04-08 Make motor drivers and omniwheels classes instead of structs
2024-04-09 Add utility functions to wheels and drivers
2024-04-11 Fix PWM issue
2024-04-11 Adapt motor test to new driver
2024-04-11 Improve PwmSlice handling of different frequencies
2024-04-11 Use 25kHz for PWM to avoid noise
    [main.cpp, motor_test.cpp]
2024-04-13 Update circuit schematic
    The new version is optimized for a protoboard
    and includes the IMU
2024-04-13 Adapt to new circuit layout
2024-04-17 Make PwmSlice a class
2024-04-17 Implement motor decoder
2024-04-19 Implement velocity measurement
2024-04-20 Implement PID controller
2024-04-20 Make motor driver methods non-const
2024-04-20 Use milliseconds in PID controller
2024-04-20 Delete copy and assignment methods for PwmSlice and MotorDecoder
    These objects shouldn't be copied as they have setup and teardown code that should only be executed once
2024-04-20 Fix some PID controller issues
2024-04-20 Implement PID driver
2024-04-23 Add motor position measurement
2024-04-23 Implement PID controller logging and tuning
2024-04-24 Add set_frequency to motor drivers
2024-04-24 Improve velocity measurement
2024-04-24 Add velocity test and improve decoder test
2024-04-24 Update robot CAD model
    [Robot.step]
2024-04-24 Fix debug guards
    Previously they weren't aligned with the cmake build type
    [motor_driver_pid.cpp]
2024-04-24 Don't use categories for PID controllers anymore
    Instead, each controller can be adjusted individually
2024-04-24 Improve PID controller test
2024-04-25 Move pico_w board setting to CMakeLists
2024-04-29 Add direction swap to motor driver
    [main.cpp]
2024-05-06 Add capacitors to schematic
2024-05-13 Implement IMU connection
2024-05-14 Refactor PID controller to use flexible timing
2024-05-15 Scale imu output
2024-05-16 Update robot CAD files
    [Robot Parts - Case Plug 1.stl, Robot Parts - Case Plug 2.stl, Robot Parts - Case Plug 3.stl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]
2024-05-16 Adjust sample times and max motor speed
2024-05-16 Make PID controller movable
2024-05-16 Implement balancing loop
    There are still problems with using the second core for the bluetooth functionality
    [main.cpp, omniwheel.cpp, robot.h]
2024-05-16 Fix omniwheel direction issue
    [omniwheel.cpp]
2024-05-16 Update BOM
2024-05-17 Use LP acceleration filter
2024-05-18 Add IMU calibration
2024-05-21 Use interrupts for robot updates
2024-05-21 Add reset method to PID controller
2024-05-21 Fix switch between ground and balance mode
    [main.cpp, omniwheel.cpp, robot.h]
2024-05-22 Implement lowpass filter options for IMU
2024-05-22 Fix balance PID input values
    Now the input is the gravity influence on the given axis
    [robot.h]
2024-05-22 Make multicore usage explicit for parameters
    This hopefully eliminates the problems experienced when including pico_multicore twice
    [decoder_test.cpp, pid_driver_test.cpp, velocity_test.cpp]
2024-05-22 Make pid parameter registration optional
2024-05-23 Revert gravity influence calculation
    Just using the down vector was correct after all
    [robot.h]
2024-05-23 Print params in serial_io
2024-05-26 Fix pid parameter registration bug
2024-05-26 Fix oscillating velocity measurement at high polling frequencies
2024-05-27 Attempt to improve velocity reading
    The idea is to support higher compute frequencies by using previous velocity value if there was no tick detected between computes
2024-05-27 Fix velocity measurement issue
2024-05-27 Don't use multicore for PID driver test
2024-05-27 Add kickstart driver
2024-05-27 Use unique pointers for driver wrappers
2024-05-28 Improve kickstart driver
2024-05-28 Fix kickstart driver issues
    [main.cpp, motor_driver_kickstart.cpp]
2024-05-28 Implement low pass filter
2024-05-29 Use LP filter only for derivative
2024-05-29 Add lp filter to robot
2024-05-30 Add velocity measurement and use it for balancing
2024-05-30 Use lp filter in velocity measurement
2024-05-30 Make kickstart test with all wheels
2024-05-31 Remove encoder term
2024-06-01 Make filter generic
2024-06-01 Add auto calibration
2024-06-01 Revert "Make filter generic"
    This reverts commit a0c6d567d426ae4b7c540cad3b4594f7bd42e6bb.
    [robot.h]
2024-06-01 Revert "Add auto calibration"
    This reverts commit 0758ad22a58ccad40a67e5f64e8832699b84aa4c.
    [main.cpp, robot.h]
2024-06-02 Fix rotation measurement bug
    [omniwheel.cpp]
2024-06-02 Add unfiltered velocity measurement
2024-06-03 Fix nullptr dereference bug
    [main.cpp]
2024-06-03 Use gyrosensor for angle estimate
2024-06-03 Extract I2C functionality into separate class
2024-06-03 Add Magnetometer
2024-06-03 Calibrate magnetometer
2024-06-04 Add z axis of magnetometer
2024-06-04 Implement 3-axis orientation and magnetometer based z angle
